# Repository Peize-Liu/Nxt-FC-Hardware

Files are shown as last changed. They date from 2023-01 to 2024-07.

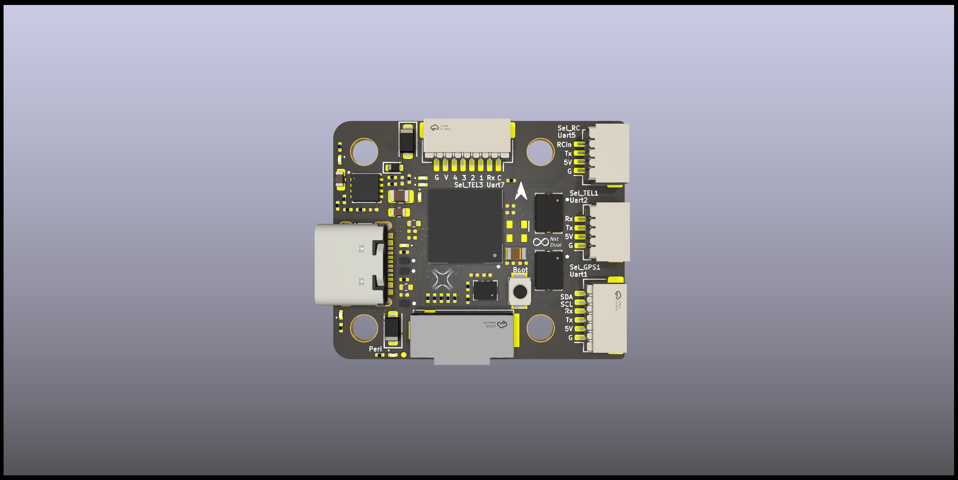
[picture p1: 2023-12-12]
NxtPX4SocketFront.png

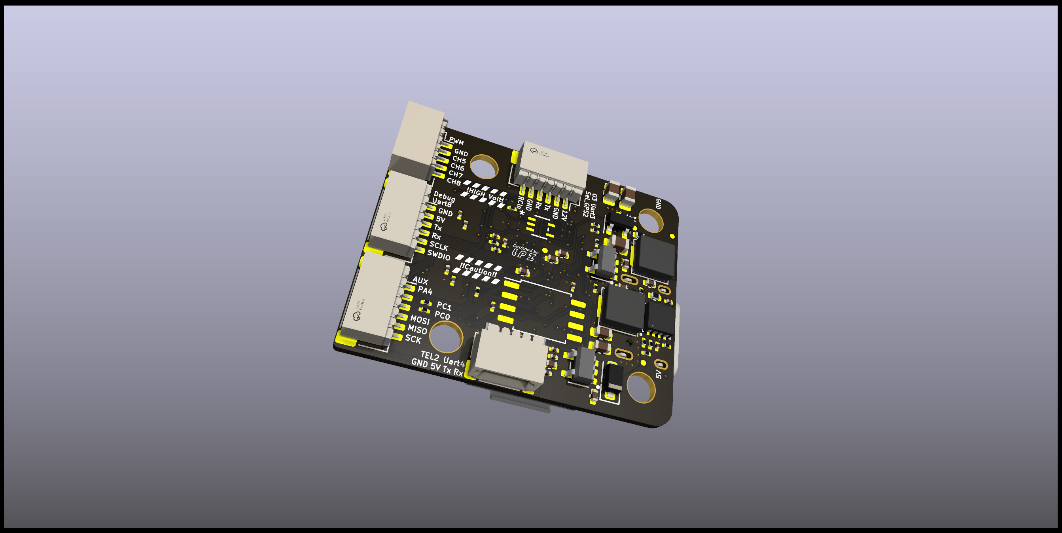
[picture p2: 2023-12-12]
NxtPX4_Back.png

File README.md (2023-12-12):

# NxtPX4-Hardware V2 Dual

* [English](# Getting start)
* [中文](# 配置指南)



## Getting start



### Hardware connection

### Compile PX4 bootloader

### Compile PX4 Firmware

### Config NxtPX4-Dual

## 配置指南



### 电控系统连接

### 编译PX4固件Bootloader

### 编译PX4固件

### 配置你的NxtPX4-Dual

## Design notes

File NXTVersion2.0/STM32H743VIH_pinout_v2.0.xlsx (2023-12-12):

STM32 H743 VIH (2MFlash 1M RAM) LBGA 封装安排不同 |  |  | 系统规定，不方便换PIN
 |  |  | 用户规定，方便换PIN，基本是外部中断和GPIO_Output
Core |  |  |  |  |  |  | 原理图检查 | STM32Cube 检查
IMU | BMI088 |  | SPI1 | MOSI | PA7 |  | v | v
 |  |  |  | MISO | PA6 |  | v | v
 |  |  |  | SCK | PA5 |  | v | v
 |  |  |  | Gyro_CS | PA3 |  | v | v
 |  |  |  | Accel_CS | PA2 |  | v | v
 |  |  |  | Gyro_Data_RDY | PA1 | EXTI1 | v | v
 |  |  |  | Accel_Data_RDY | s | EXTI0 | v | v
 | BMI088 |  | SPI4 | MOSI | PE6 |  | v | v
 |  |  |  | MISO | PE5 |  | v | v
 |  |  |  | SCK | PE2 |  | v | v
 |  |  |  | Gyro_CS | PC2 |  | v | v
 |  |  |  | Accel_CS | PC13 |  | v | v
 |  |  |  | Gyro_Data_RDY | PE3 | EXTI3 | v | v
 |  |  |  | Accel_Data_RDY | PE4 | EXTI4 | v | v
Baro | SPL06-01 |  | I2C1 | SDA | PB7 |  | v | v
 |  |  |  | SCL | PB6 |  | v | v
 |  |  |  | Baro_Data_RDY | PB5 | EXTI5 | v | v
Motor | PWM/DSHOT | CH1 | TIM1 | CH1 | PE9 |  | v | v
 |  | CH2 |  | CH2 | PE11 |  | v | v
 |  | CH3 |  | CH3 | PE13 |  | v | v
 |  | CH4 |  | CH4 | PE14 |  | v | v
 |  | CH5 | TIM2 | CH3 | PB10 |  | v | v
 |  | CH6 |  | CH4 | PB11 |  | v | v
 |  | CH7 | TIM3 | CH3 | PB0 |  | v | v
 |  | CH8 |  | CH4 | PB1 |  | v | v
LSE | 32.768kHz |  | OSC32 | OSC_IN | PC14 |  | v | v
 |  |  |  | OSC_OUT | PC15 |  | v | v
HSE | 16Mhz source |  | OSC | OSC_IN | PH0 |  | v | v
LED | GPIO_OUTPUT |  | Blue |  | PB15 |  | v | v
 |  |  | Red |  | PD15 |  | v | v
 |  |  | Green |  | PD11 |  | v | v
FRAM | W25Q128JVS |  | SPI2 | SCK | PD3 |  | v | v
 |  |  |  | MISO | PB14 |  | v | v
 |  |  |  | MOSI | PC3 |  | v | v
 |  |  |  | CS | PD4 |  | v | v
Connector
SPI |  |  | SPI3 | MOSI | PB2 |  | v | v
 |  |  |  | MISO | PB4 |  | v | v
 |  |  |  | SCK | PB3 |  | v | v
I2C |  |  | I2C4 | SDA | PD13 |  | v | v
 |  |  |  | SCL | PD12 |  | v | v
UART | Debug (GPS3) |  | UART8 | RX | PE0 |  | v | v
 |  |  |  | TX | PE1 |  | v | v
 | Computer (TEL1) |  | UART4 | RX | PB8 |  | v | v
 |  |  |  | TX | PB9 |  | v | v
 | RC_input(RC) |  |  | Sbus INV | PD14 |  | v | v
 |  |  | UART5 | RX | PB12 |  | v | v
 |  |  |  | TX | PB13 |  | v | v
 | Debug (NC) |  | UART6 | RX | PC7 |  | v | No hardware connection support
 |  |  |  | TX | PC6 |  | v
 | ESC_tele(TEL2) |  | UART7 | RX | PE7 |  | v | v
 |  |  |  | TX | PE8 | NC | v | v
 |  |  | USART1 | CK | PA8 | NC | v
 | GPS1 |  |  | TX | PA9 |  | v | v
 |  |  |  | RX | PA10 |  | v | v
 |  |  | USART2 | CK | PD7 | NC | v
 | GPS2 |  |  | TX | PD5 |  | v | v
 |  |  |  | RX | PD6 |  | v | v
 |  |  | USART3 | CK | PD10 | NC | v
 | TEL3 |  |  | TX | PD8 |  | v | v
 |  |  |  | RX | PD9 |  | v | v
USB_FS |  |  | USB | FS_DM | PA11 |  | v | v
 |  |  |  | FS_DP | PA12 |  | v | v
SD |  |  | SDMMC1 | D0 | PC8 |  | v | v
 |  |  |  | D1 | PC9 |  | v | v
 |  |  |  | D2 | PC10 |  | v | v
 |  |  |  | D3 | PC11 |  | v | v
 |  |  |  | CK | PC12 |  | v | v
 |  |  |  | CMD | PD2 |  | v | v
Debug |  |  | SWD | SWDIO | PA13 |  | v | v
 |  |  |  | SWCLK | PA14 |  | v | v
Battery |  |  | ADC1_INP4 | BAT_V | PC4 |  | v | v
 |  |  | ADC2_INP8 | BAT_I | PC5 |  | v | v
USB Detection |  |  | Input |  | PD0 |  | v | v
AUX_GPIO |  |  |  | AUX1 | PC0 |  | v | v
 |  |  |  | AUX2 | PC1 |  | v | v
 |  |  |  | AUX3 | PA4 |  | v | v

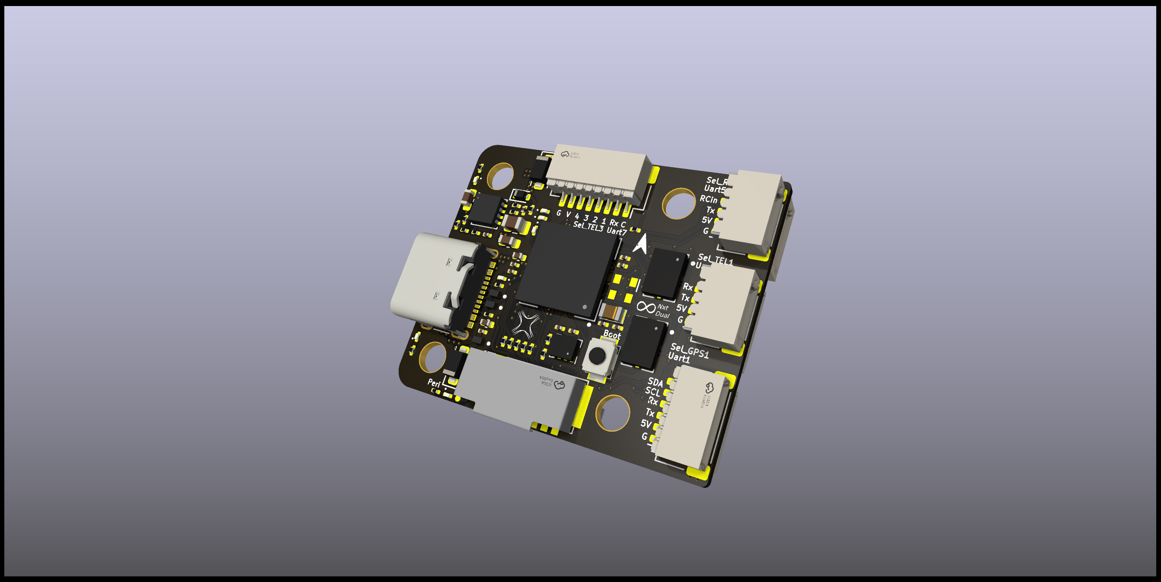
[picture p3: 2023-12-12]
NxtPX4_Front.png

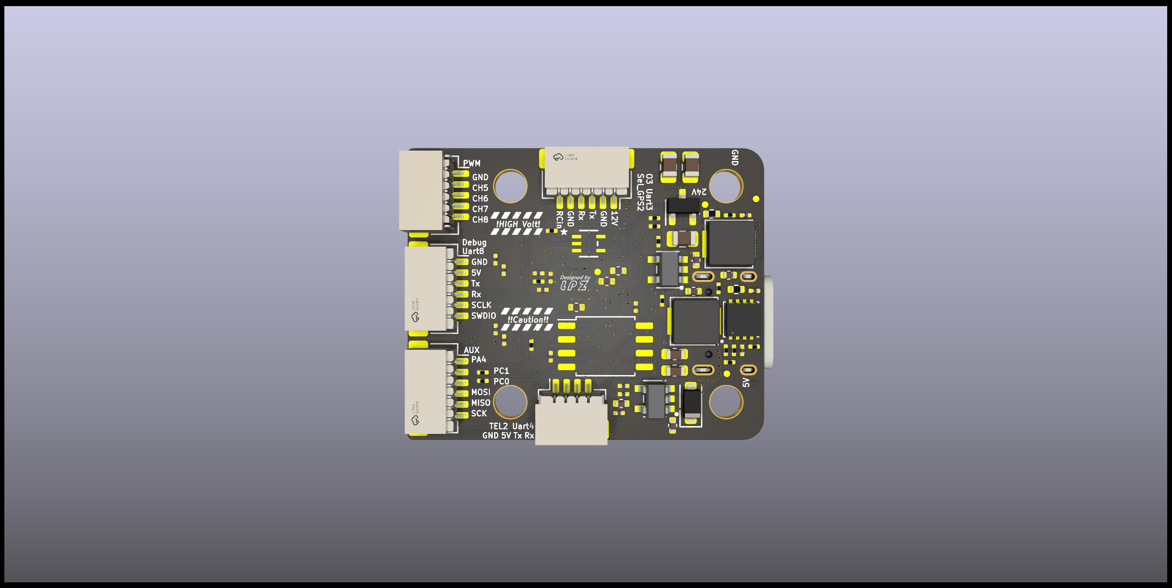
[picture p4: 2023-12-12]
NxtPX4SocketBack.png

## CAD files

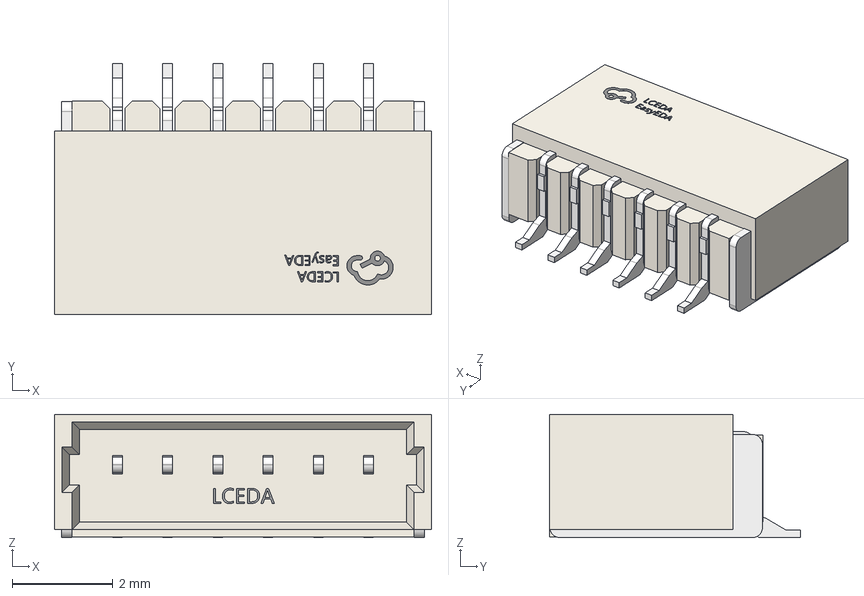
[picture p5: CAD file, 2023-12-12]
NxtFC-DUAL/project_lib/3D_Model/sh1.0_6pin_hori.step
7.50 x 5.00 x 2.45 mm

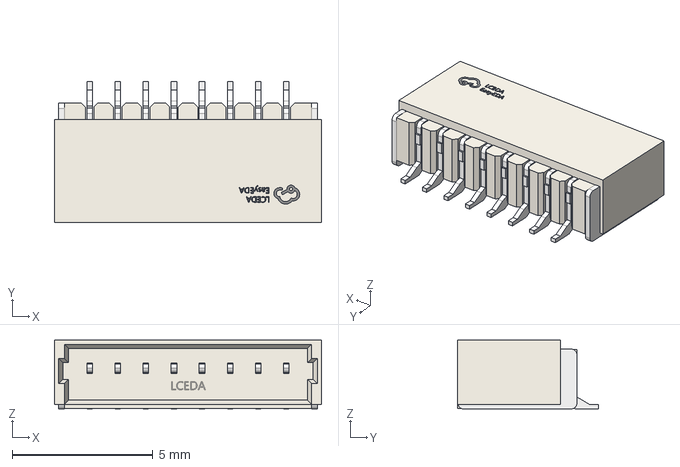
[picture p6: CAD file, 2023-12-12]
NxtFC-DUAL/project_lib/3D_Model/sh1.0_8p_hori.step
9.50 x 5.00 x 2.45 mm

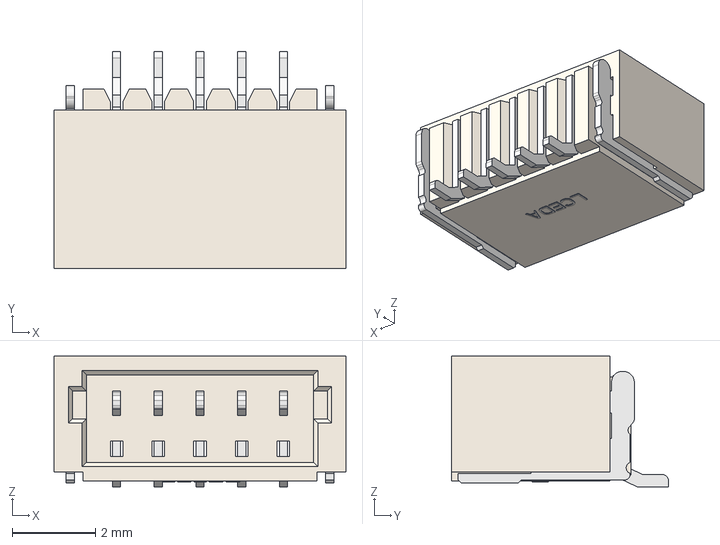
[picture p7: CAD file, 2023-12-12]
NxtFC-DUAL/project_lib/3D_Model/sh1.0_5pin_hori.step
7.00 x 5.20 x 3.14 mm

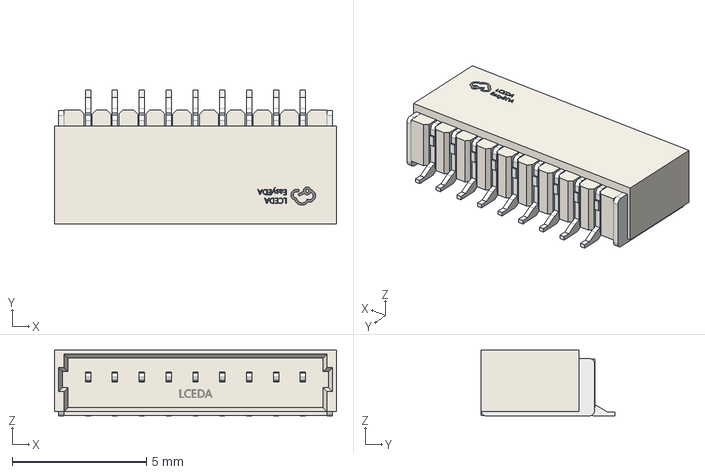
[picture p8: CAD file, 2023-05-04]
NxtFC-DUAL/project_lib/3D_Model/sh1.0_01x09_hori.step
10.5 x 5.00 x 2.45 mm

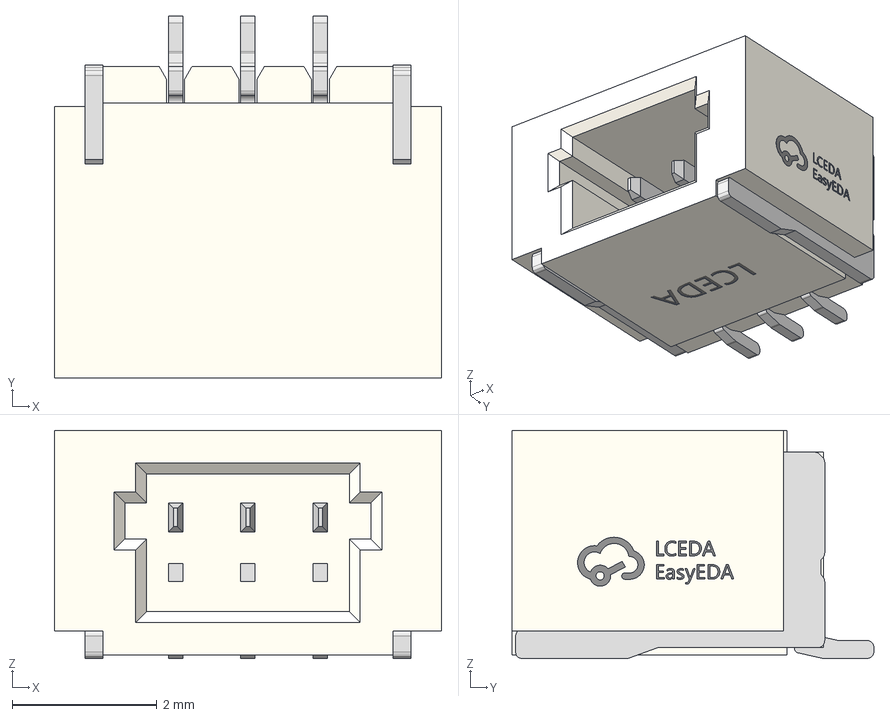
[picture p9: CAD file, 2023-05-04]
NxtFC-DUAL/project_lib/3D_Model/sh1.0_3pin_hor.step
5.35 x 5.00 x 3.15 mm

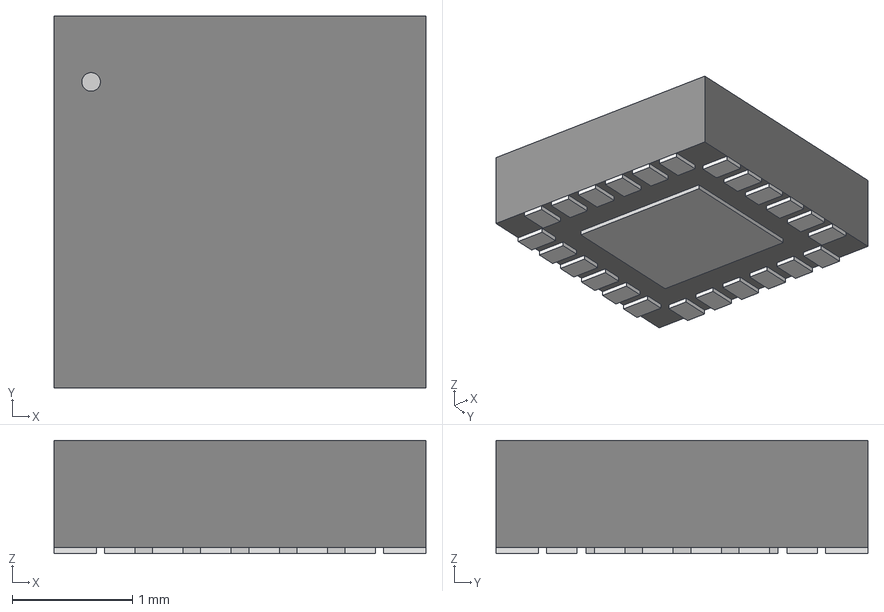
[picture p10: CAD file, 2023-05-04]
NxtFC-DUAL/project_lib/3D_Model/QFN24_3X3X0P9_IVS_ICM20649.step
3.10 x 3.10 x 0.942 mm

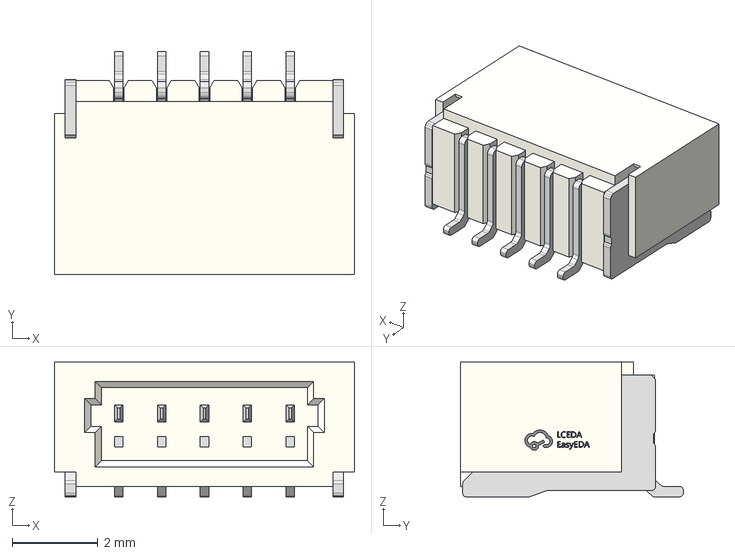
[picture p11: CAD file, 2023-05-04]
NxtFC-DUAL/project_lib/3D_Model/01x05_sh1.0_hori.step
7.00 x 5.20 x 3.15 mm

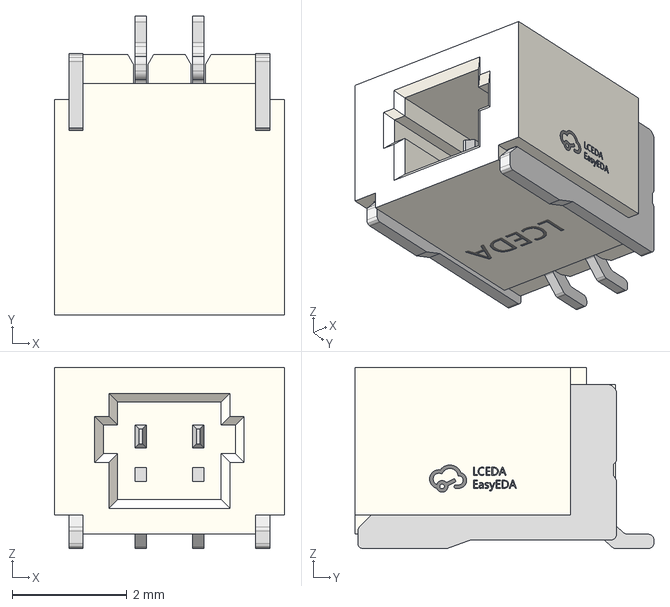
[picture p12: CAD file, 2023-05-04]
NxtFC-DUAL/project_lib/3D_Model/sh1.0_01x02p_hori.step
4.00 x 5.20 x 3.15 mm

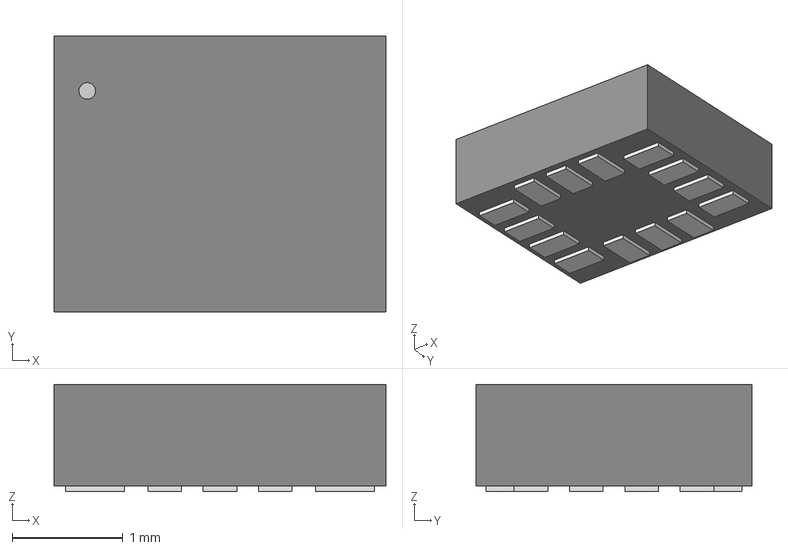
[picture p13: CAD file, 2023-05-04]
NxtFC-DUAL/project_lib/3D_Model/LGA14_2P5X3X0P91_IVS_ICM42688-P .step
3.00 x 2.49 x 0.968 mm

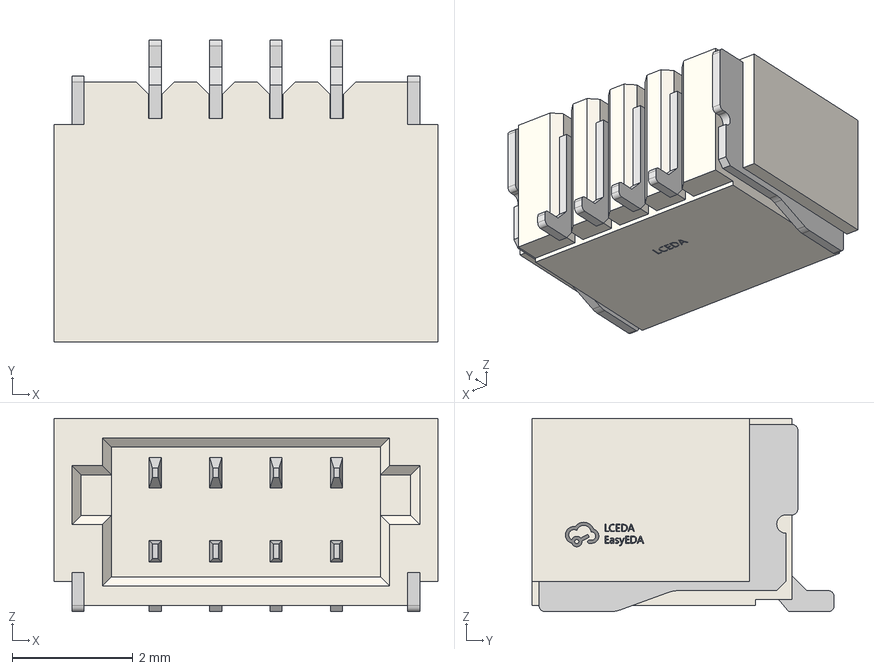
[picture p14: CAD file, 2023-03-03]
NxtFC-DUAL/project_lib/3D_Model/sh1.0_4p.step
6.35 x 5.00 x 3.20 mm

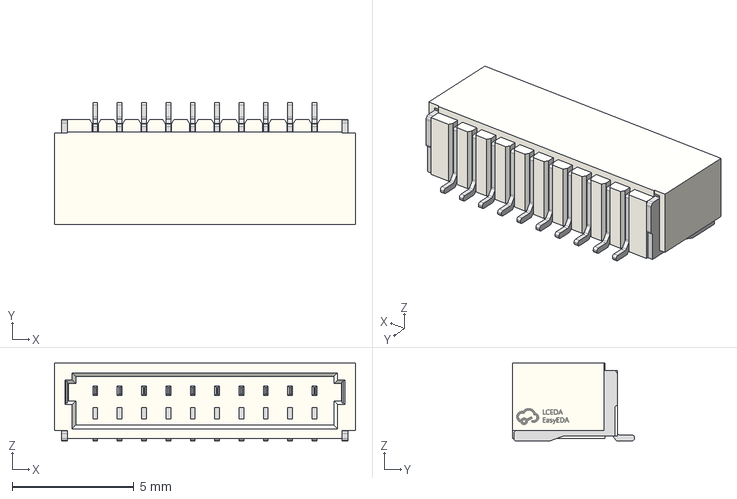
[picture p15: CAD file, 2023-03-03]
NxtFC-DUAL/project_lib/3D_Model/sh1.0_10P.step
12.4 x 5.00 x 3.20 mm

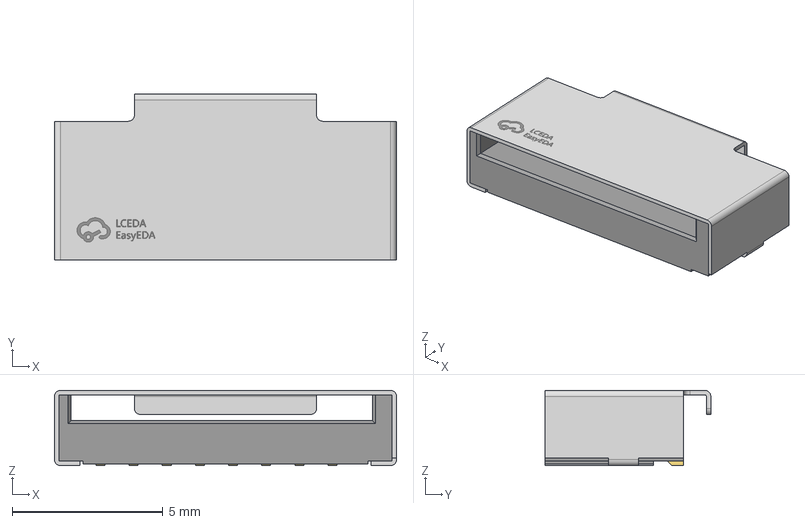
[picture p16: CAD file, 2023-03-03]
NxtFC-DUAL/project_lib/3D_Model/sd_card.step
11.4 x 5.50 x 2.50 mm

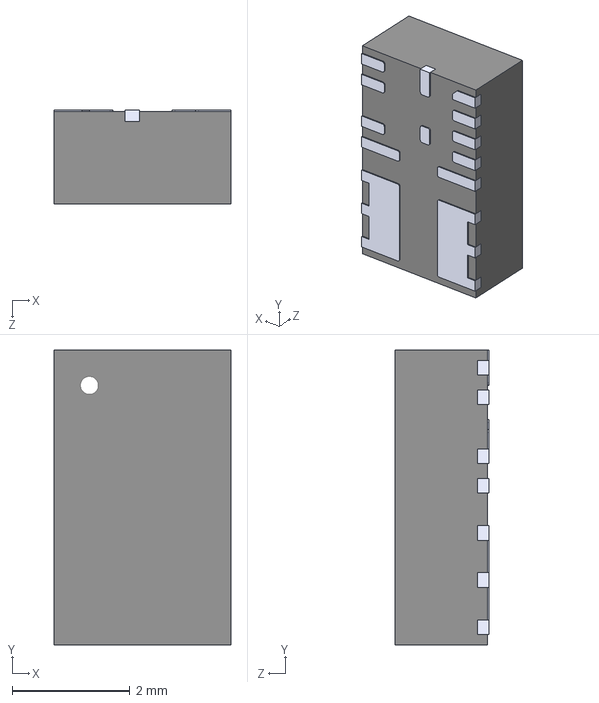
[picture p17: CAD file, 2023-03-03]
NxtFC-DUAL/project_lib/3D_Model/MPM3515GQV-AEC1 (QFN-17, 3x5x1.6).step
3.00 x 5.00 x 1.60 mm

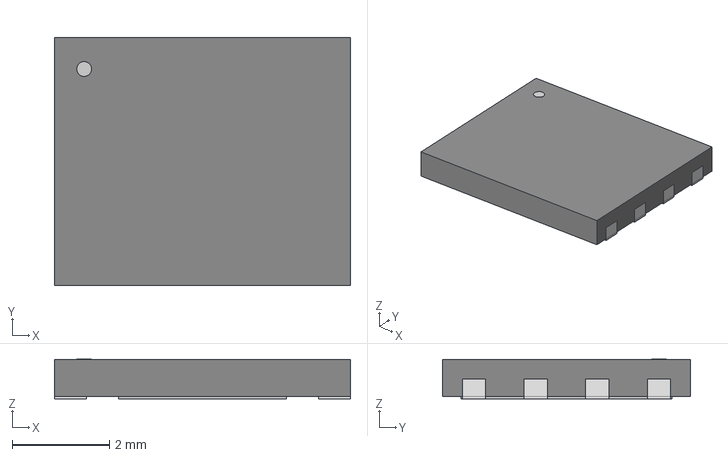
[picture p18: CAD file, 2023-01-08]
NxtFC-DUAL/project_lib/3D_Model/WSON-8_6X5_WIN.step
6.10 x 5.11 x 0.815 mm

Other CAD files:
NxtFC-DUAL/project_lib/3D_Model/CAP_ABS07-32_768KHZ-T_ABR.step
NxtFC-DUAL/project_lib/3D_Model/DFN1006-2_SOD882_NEX.step
NxtFC-DUAL/project_lib/3D_Model/QFN_BMP388_BOS.step
NxtFC-DUAL/project_lib/3D_Model/CSP-USC16-TR--3DModel-STEP-468060.STEP
NxtFC-DUAL/project_lib/3D_Model/QFN8_3X3_MPS.step
NxtFC-DUAL/project_lib/3D_Model/SG-210STF25_0000ML3_EPS.step
NxtFC-DUAL/project_lib/3D_Model/SOT-23-5_RIT.step
NxtFC-DUAL/project_lib/3D_Model/TFBGA100.step

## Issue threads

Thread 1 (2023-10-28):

ETH support planned?

petergerten, 2023-10-28:
Hi,

great project!
Any plans for a revision with ethernet mac support for fast communication with companion computer?

Peter

Peize-Liu, 2023-10-28:
Hello,
Thank you for your advice, current version provides IMU message at 500Hz using maximum baudrate. The maximum control rate and message rate are limited by MCU frequncy and also PX4 firmware. I don't think there is a need for ethernet mac in Nxt, because of the PCB size and also the task of our research. But if there is a need for that, I may seek for some cooperation to achive that.

Closed 2023-10-28.

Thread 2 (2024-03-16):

你好，为什么在第二个版本中没有使用icm42688 ，而是使用两个bmi088

deepuav, 2024-03-16:
从参数上看icm42688 要优于 bmi088啊，是不是不稳定啊？

Peize-Liu, 2024-03-17:
ICM 系列都挺容易震傻，BMI088 测下来在当前我们所有的飞机结构上，数据更好一些

deepuav, 2024-03-20:
感谢大神回复。这边pps输入捕获功能和相机触发移植的怎么样啊？有测试过吗？

Peize-Liu, 2024-03-20:
> 感谢大神回复。这边pps输入捕获功能和相机触发移植的怎么样啊？有测试过吗？

没有这样搞过，如果PX4 固件支持的话，硬件上应该只要有可以使用的GPIO都是可以的，我们系统IMU和相机不是同步的，所以没有特别考虑过

deepuav, 2024-03-20:
我这边在您第二版的基础上加了一个adis16470，把一个bmi088换成了icm42686 。想做板子测试一下，需要您这边许可吗？

deepuav, 2024-03-20:
>
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

deepuav, 2024-03-20:
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

deepuav, 2024-03-20:
回头我把kicad工程，也发上来

deepuav, 2024-03-21:
13176502829 我把工程文件打包发给你

hcws, 2025-08-09:
Thank you for your contribution. May I ask why the BOM and Gerber files for version V2 were not generated?

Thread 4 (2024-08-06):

v1.2.0 schematics

raimapo, 2024-08-06:
Hello,

Will You provide v1.2.0 schematics and PCB. I will be glad to test this autopilot, but I need to change connectors which could be more suitable for my project. Thank You.

Raimondas

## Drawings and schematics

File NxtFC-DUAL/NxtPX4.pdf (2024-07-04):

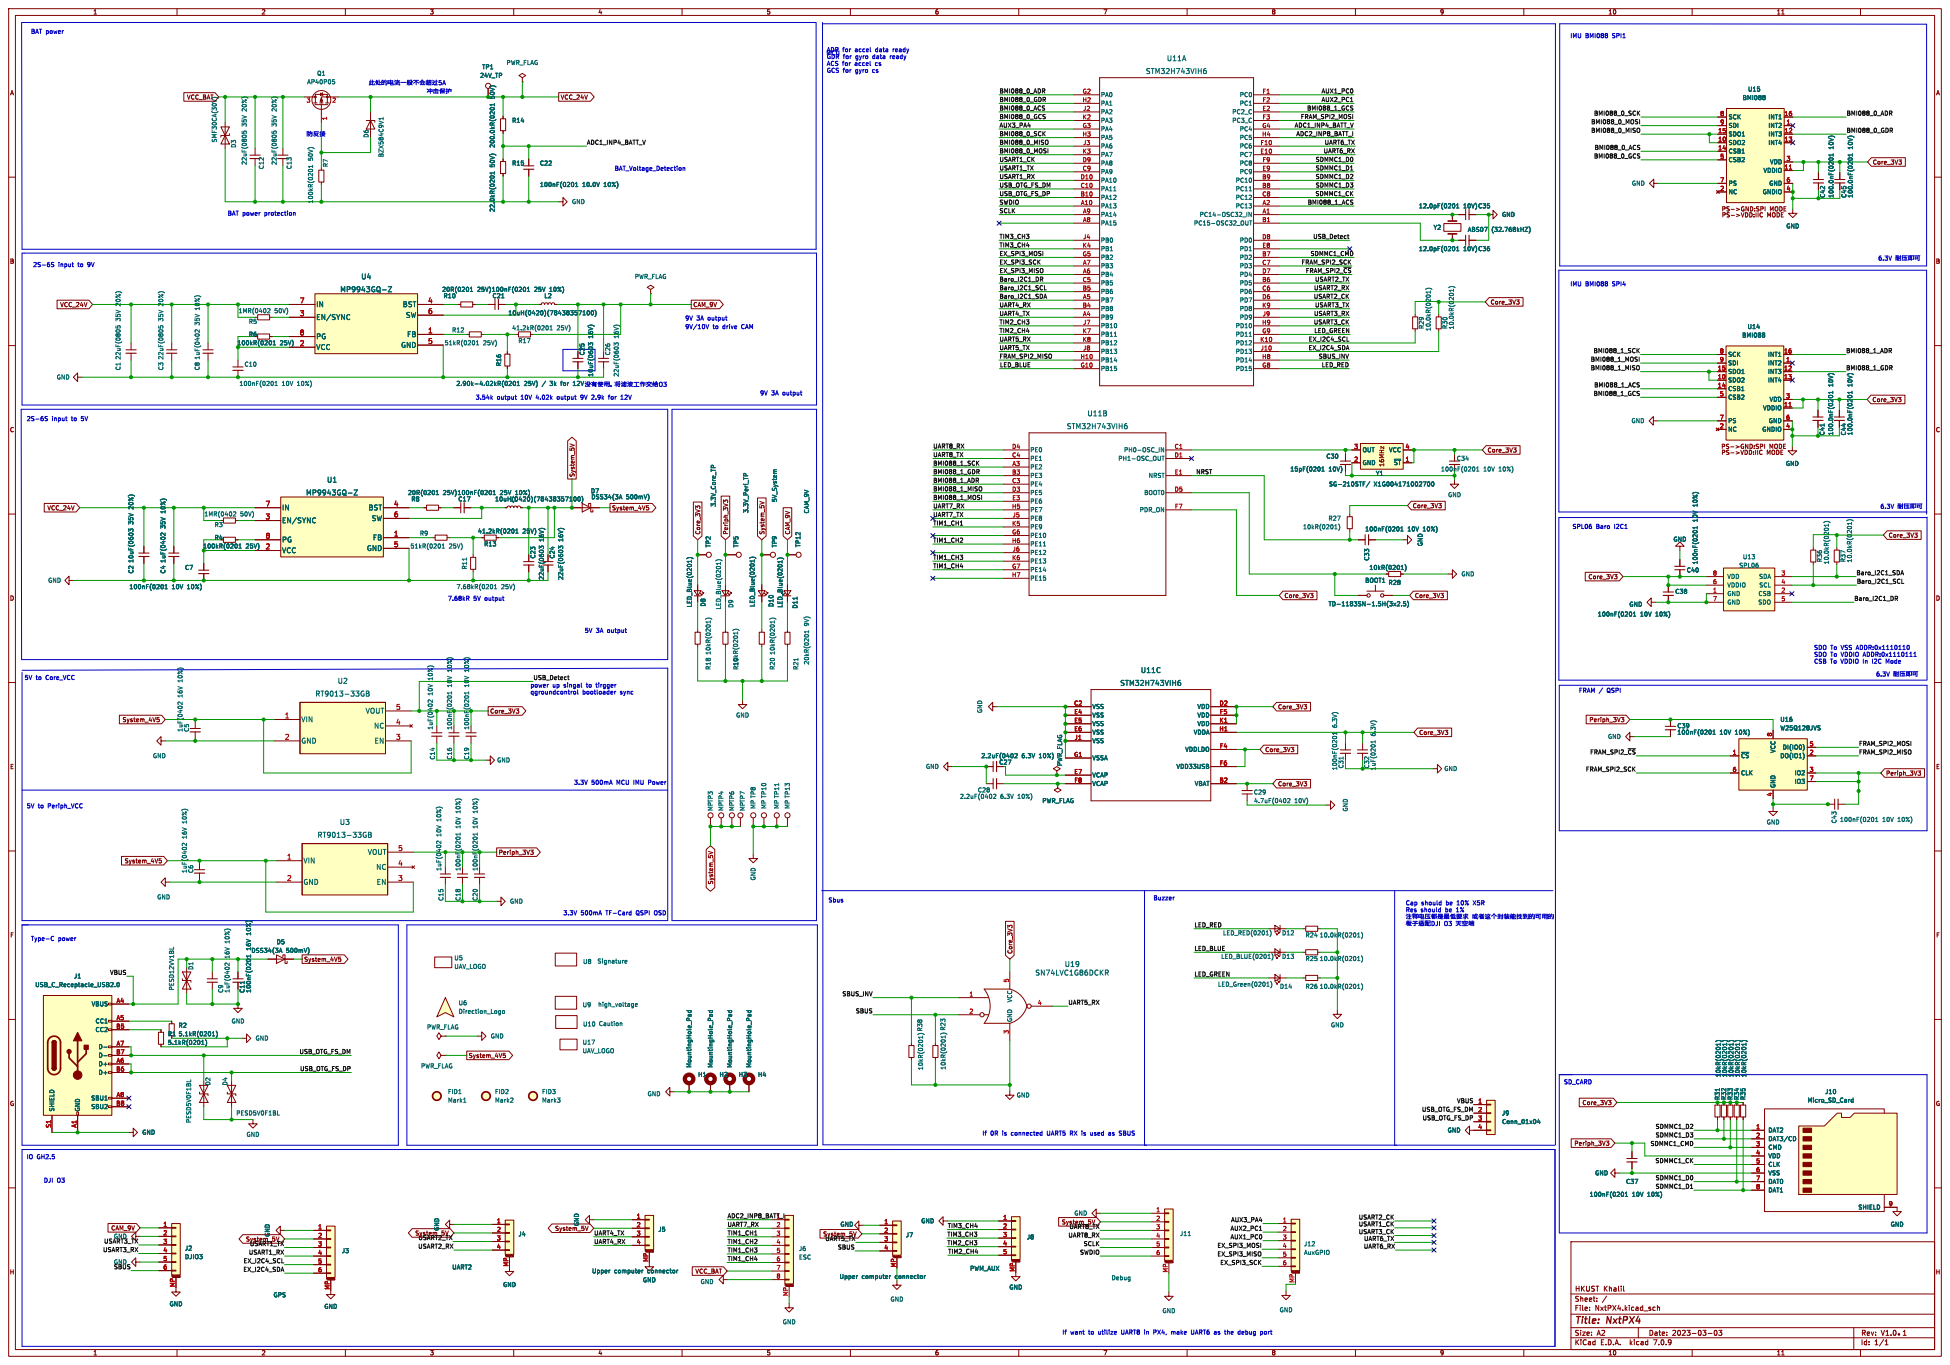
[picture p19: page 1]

ADR for accel data ready GDR for gyro data ready ACS for accel cs GCS for gyro cs
MCU

9V 3A output þÿl¡g O•u(ÿ\nälâ]åO\N¤~ÙO3

SDO To VSS ADDR:0x1110110 SDO To VDDIO ADDR:0x1110111 CSB To VDDIO In I2C Mode

power up singal to tirgger

Cap should be 10% X5R
Res should be 1%
þÿlè‘Êu5S‹•ýf/gON‰•lB þÿb€•ÙN*\ˆÅ€ýb~R0v„Sïu(v„
þÿg•[P•-

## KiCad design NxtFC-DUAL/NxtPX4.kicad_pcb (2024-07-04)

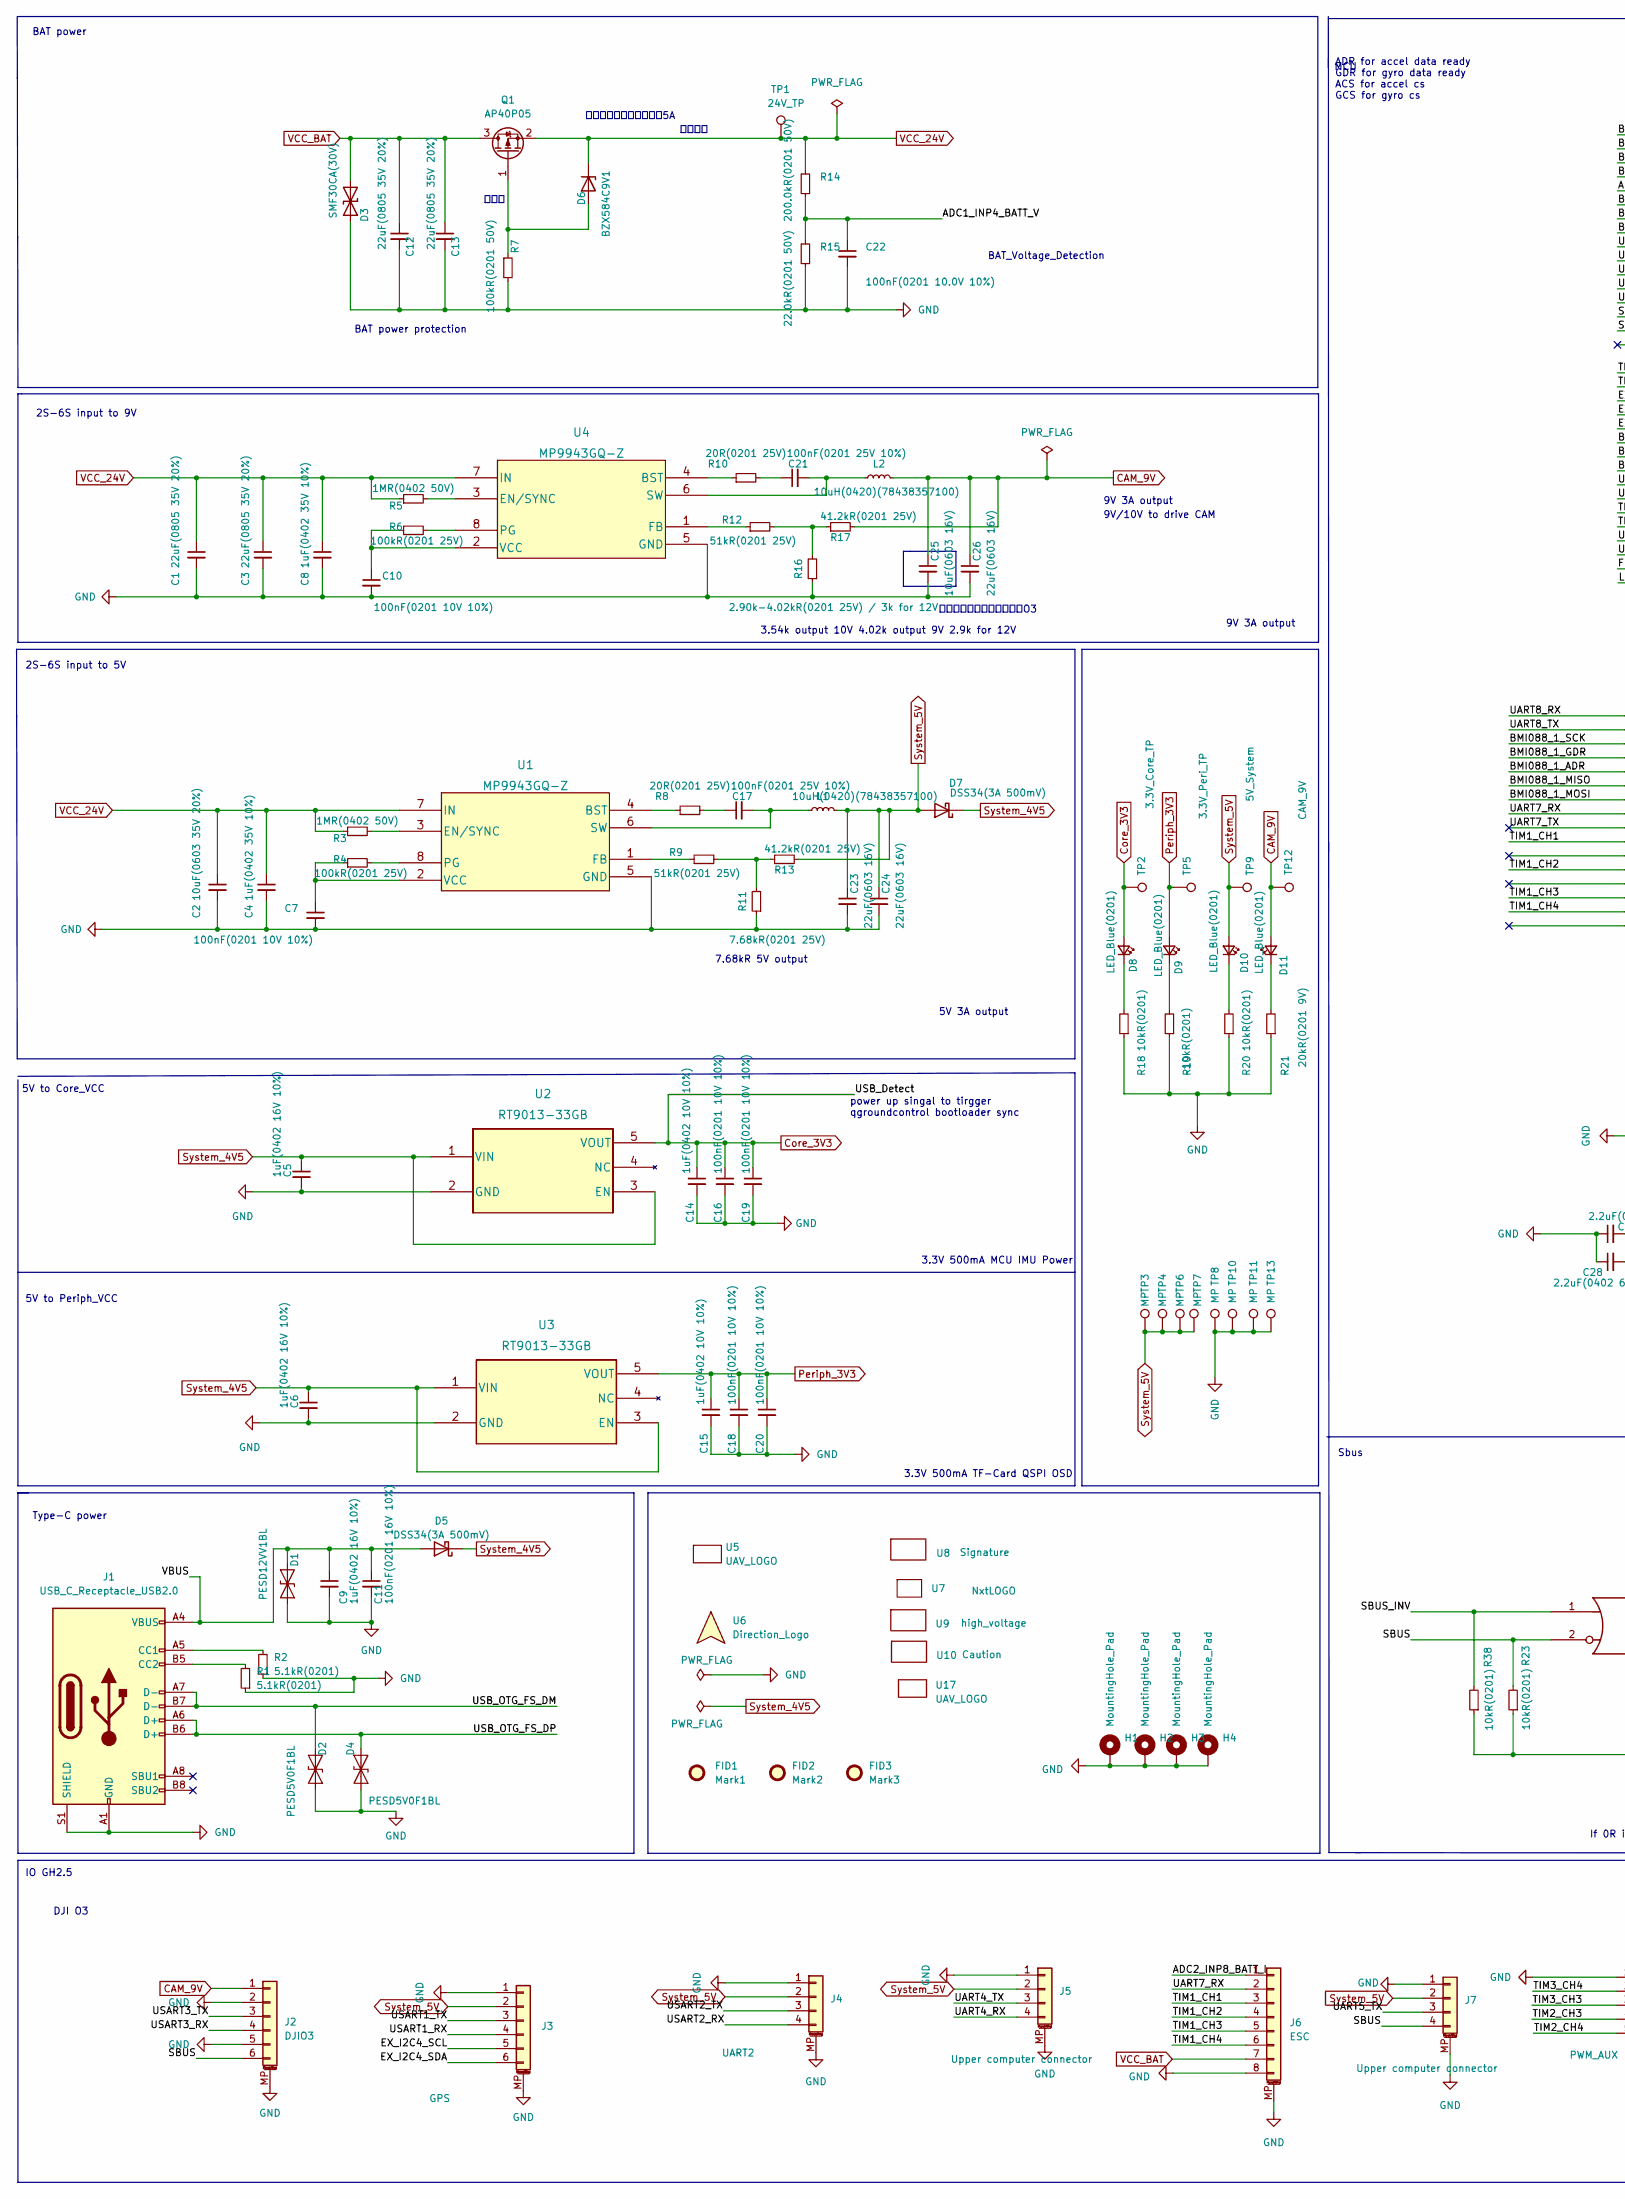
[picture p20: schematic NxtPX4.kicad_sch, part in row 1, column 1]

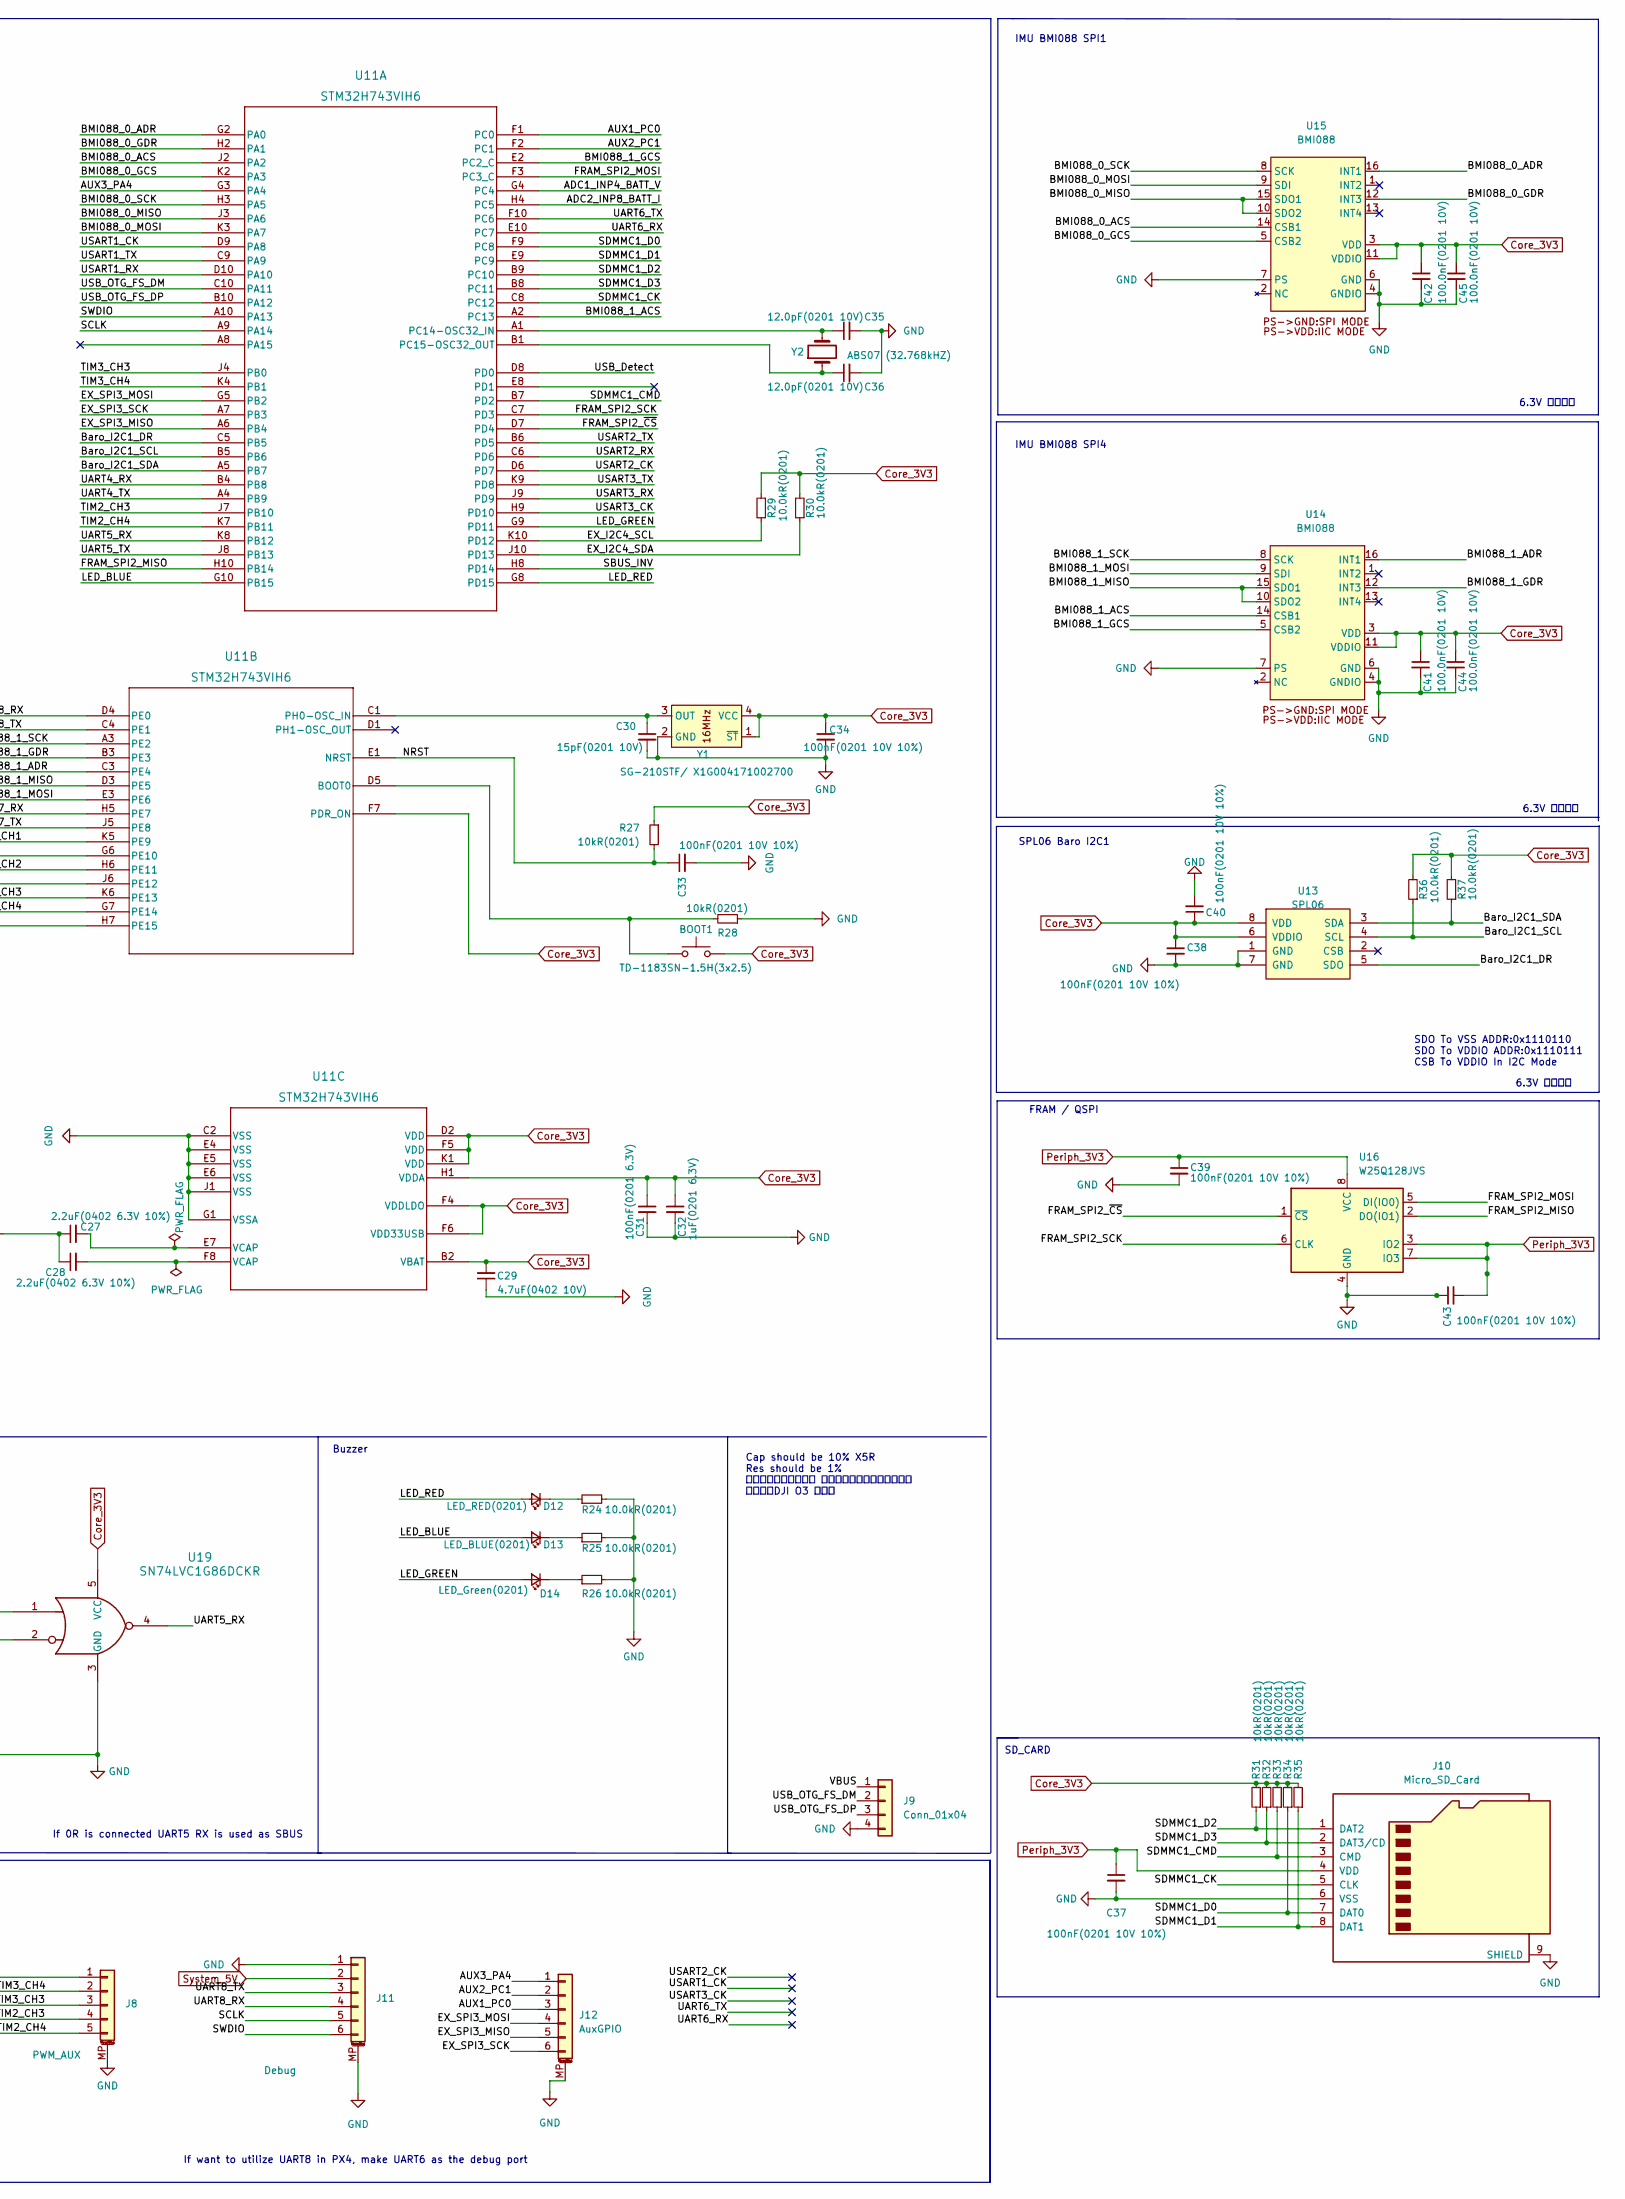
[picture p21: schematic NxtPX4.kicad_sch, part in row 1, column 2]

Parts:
BOOT1: TD-1183SN-1.5H(3x2.5); 3x2.5PushButton
C1, C3, C12, C13: 22uF(0805 35V 20%); C_0805_2012Metric
C2: 10uF(0603 35V 20%); C_0603_1608Metric
C4, C8: 1uF(0402 35V 10%); C_0402_1005Metric
C5, C6, C9: 1uF(0402 16V 10%); C_0402_1005Metric
C7, C10, C16, C18, C19, C20, C33, C34, C37, C38, C39, C40, C43: 100nF(0201 10V 10%); C_0201_0603Metric
C11: 100nF(0201 16V 10%); C_0201_0603Metric
C14, C15: 1uF(0402 10V 10%); C_0402_1005Metric
C17, C21: 100nF(0201 25V 10%); C_0201_0603Metric
C22: 100nF(0201 10.0V 10%); C_0201_0603Metric
C23, C24, C26: 22uF(0603 16V); C_0603_1608Metric
C25: 10uF(0603 16V); C_0603_1608Metric
C27, C28: 2.2uF(0402 6.3V 10%); C_0402_1005Metric
C29: 4.7uF(0402 10V); C_0402_1005Metric
C30: 15pF(0201 10V); C_0201_0603Metric
C31: 100nF(0201 6.3V); C_0201_0603Metric
C32: 1uF(0201 6.3V); C_0201_0603Metric
C35, C36: 12.0pF(0201 10V); C_0201_0603Metric
C41, C42, C44, C45: 100.0nF(0201 10V); C_0201_0603Metric
D1: PESD12VV1BL; PESD12VV1BL_315
D2, D4: PESD5V0F1BL
D3: SMF30CA(30V); D_SOD-123F
D5, D7: DSS34(3A 500mV); D_SOD-123F
D6: BZX584C9V1; D_SOD-523
D8, D9, D10, D11: LED_Blue(0201); LED_0201_0603Metric
D12: LED_RED(0201); LED_0201_0603Metric
D13: LED_BLUE(0201); LED_0201_0603Metric
D14: LED_Green(0201); LED_0201_0603Metric
FID1: Mark1; Fidiucial
FID2: Mark2; Fidiucial
FID3: Mark3; Fidiucial
H1, H2, H3, H4: MountingHole_Pad; M2MountingHole
J1: USB_C_Receptacle_USB2.0; USB_C_Small
J2: DJIO3; 1x06-1MP_P1.00mm_Horizontal
J3: GPS; 1x06-1MP_P1.00mm_Horizontal
J4: UART2; 01x04_MP_sh1.0_Hori
J5, J7: Upper computer connector; 01x04_MP_sh1.0_Hori
J6: ESC; 01x08_MP_sh1.0_Hori
J8: PWM_AUX; 01x05_MP_sh1.0_Hori
J9: Conn_01x04; Conn_4Pin
J10: Micro_SD_Card; TF-SMD_TF-021B-H265
J11: Debug; 1x06-1MP_P1.00mm_Horizontal
J12: AuxGPIO; 1x06-1MP_P1.00mm_Horizontal
L1, L2: 10uH(0420)(78438357100); Inductor_0420
Q1: AP40P05; SOT-23
R1, R2: 5.1kR(0201); R_0201_0603Metric
R3, R5: 1MR(0402 50V); R_0402_1005Metric
R4, R6: 100kR(0201 25V); R_0201_0603Metric
R7: 100kR(0201 50V); R_0201_0603Metric
R8, R10: 20R(0201 25V); R_0201_0603Metric
R9, R12: 51kR(0201 25V); R_0201_0603Metric
R11: 7.68kR(0201 25V); R_0201_0603Metric
R13, R17: 41.2kR(0201 25V); R_0201_0603Metric
R14: 200.0kR(0201 50V); R_0201_0603Metric
R15: 22.0kR(0201 50V); R_0201_0603Metric
R16: 2.90k-4.02kR(0201 25V) / 3k for 12V; R_0201_0603Metric
R18, R19, R20, R23, R27, R28, R31, R32, R33, R34, R35, R38: 10kR(0201); R_0201_0603Metric
R21: 20kR(0201 9V); R_0201_0603Metric
R24, R25, R26, R29, R30, R36, R37: 10.0kR(0201); R_0201_0603Metric
TP1: 24V_TP; MiniTP
TP2: 3.3V_Core_TP; MiniTP
TP3, TP4, TP6, TP7, TP8, TP10, TP11, TP13: MP; PWR_Circle
TP5: 3.3V_Peri_TP; MiniTP
TP9: 5V_System; MiniTP
TP12: CAM_9V; MiniTP
U1, U4: MP9943GQ-Z
U2, U3: RT9013-33GB
U5: UAV_LOGO; Uav_logo
U6: Direction_Logo
U7: NxtLOGO
U8: Signature; my_signature
U9: high_voltage
U10: Caution
U11: STM32H743VIH6; STM32H743VIHBGA100C80P10X10_800X800X110N
U13: SPL06; Bosch_LGA-8_2x2.5mm_P0.65mm_ClockwisePinNumbering
U14, U15: BMI088
U16: W25Q128JVS; SOIC-8_5.23x5.23mm_P1.27mm
U17: UAV_LOGO; Dual_logo
U19: SN74LVC1G86DCKR; DCK5
Y1: SG-210STF/ X1G004171002700; Oscillator_SMD_Abracon_ASDMB-4Pin_2.5x2.0mm
Y2: ABS07 (32.768kHZ); LSE(2012)

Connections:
/ADC1_INP4_BATT_V: C22.1, R14.2, R15.1, U11.G4 (PC4)
/ADC2_INP8_BATT_I: J6.1, U11.H4 (PC5)
/AUX1_PC0: J12.3, U11.F1 (PC0)
/AUX2_PC1: J12.2, U11.F2 (PC1)
/AUX3_PA4: J12.1, U11.G3 (PA4)
/BMI088_0_ACS: U11.J2 (PA2), U15.14 (CSB1)
/BMI088_0_ADR: U11.G2 (PA0), U15.16 (INT1)
/BMI088_0_GCS: U11.K2 (PA3), U15.5 (CSB2)
/BMI088_0_GDR: U11.H2 (PA1), U15.12 (INT3)
/BMI088_0_MISO: U11.J3 (PA6), U15.10 (SDO2), U15.15 (SDO1)
/BMI088_0_MOSI: U11.K3 (PA7), U15.9 (SDI)
/BMI088_0_SCK: U11.H3 (PA5), U15.8 (SCK)
/BMI088_1_ACS: U11.A2 (PC13), U14.14 (CSB1)
/BMI088_1_ADR: U11.C3 (PE4), U14.16 (INT1)
/BMI088_1_GCS: U11.E2 (PC2_C), U14.5 (CSB2)
/BMI088_1_GDR: U11.B3 (PE3), U14.12 (INT3)
/BMI088_1_MISO: U11.D3 (PE5), U14.10 (SDO2), U14.15 (SDO1)
/BMI088_1_MOSI: U11.E3 (PE6), U14.9 (SDI)
/BMI088_1_SCK: U11.A3 (PE2), U14.8 (SCK)
/Baro_I2C1_DR: U11.C5 (PB5), U13.5 (SDO)
/Baro_I2C1_SCL: R36.1, U11.B5 (PB6), U13.4 (SCL)
/Baro_I2C1_SDA: R37.1, U11.A5 (PB7), U13.3 (SDA)
/EX_I2C4_SCL: J3.5, R29.1, U11.K10 (PD12)
/EX_I2C4_SDA: J3.6, R30.1, U11.J10 (PD13)
/EX_SPI3_MISO: J12.5, U11.A6 (PB4)
/EX_SPI3_MOSI: J12.4, U11.G5 (PB2)
/EX_SPI3_SCK: J12.6, U11.A7 (PB3)
/FRAM_SPI2_MISO: U11.H10 (PB14), U16.2 (DO(IO1))
/FRAM_SPI2_MOSI: U11.F3 (PC3_C), U16.5 (DI(IO0))
/FRAM_SPI2_SCK: U11.C7 (PD3), U16.6 (CLK)
/FRAM_SPI2_~CS: U11.D7 (PD4), U16.1 (~CS)
/LED_BLUE: D13.2 (A), U11.G10 (PB15)
/LED_GREEN: D14.2 (A), U11.G9 (PD11)
/LED_RED: D12.2 (A), U11.G8 (PD15)
/NRST: C33.1, R27.2, U11.E1 (NRST)
/SBUS: J2.6, J7.4, R23.2, U19.2
/SBUS_INV: R38.2, U11.H8 (PD14), U19.1
/SCLK: J11.5, U11.A9 (PA14)
/SDMMC1_CK: J10.5 (CLK), U11.C8 (PC12)
/SDMMC1_CMD: J10.3 (CMD), R33.1, U11.B7 (PD2)
/SDMMC1_D0: J10.7 (DAT0), R34.1, U11.F9 (PC8)
/SDMMC1_D1: J10.8 (DAT1), R35.1, U11.E9 (PC9)
/SDMMC1_D2: J10.1 (DAT2), R31.1, U11.B9 (PC10)
/SDMMC1_D3: J10.2 (DAT3/CD), R32.1, U11.B8 (PC11)
/SWDIO: J11.6, U11.A10 (PA13)
/TIM1_CH1: J6.3, U11.K5 (PE9)
/TIM1_CH2: J6.4, U11.H6 (PE11)
/TIM1_CH3: J6.5, U11.K6 (PE13)
/TIM1_CH4: J6.6, U11.G7 (PE14)
/TIM2_CH3: J8.4, U11.J7 (PB10)
/TIM2_CH4: J8.5, U11.K7 (PB11)
/TIM3_CH3: J8.3, U11.J4 (PB0)
/TIM3_CH4: J8.2, U11.K4 (PB1)
/UART4_RX: J5.4, U11.B4 (PB8)
/UART4_TX: J5.3, U11.A4 (PB9)
/UART5_RX: U11.K8 (PB12), U19.4
/UART5_TX: J7.3, U11.J8 (PB13)
/UART6_RX: U11.E10 (PC7)
/UART6_TX: U11.F10 (PC6)
/UART7_RX: J6.2, U11.H5 (PE7)
/UART7_TX: U11.J5 (PE8)
/UART8_RX: J11.4, U11.D4 (PE0)
/UART8_TX: J11.3, U11.C4 (PE1)
/USART1_CK: U11.D9 (PA8)
/USART1_RX: J3.4, U11.D10 (PA10)
/USART1_TX: J3.3, U11.C9 (PA9)
/USART2_CK: U11.D6 (PD7)
/USART2_RX: J4.4, U11.C6 (PD6)
/USART2_TX: J4.3, U11.B6 (PD5)
/USART3_CK: U11.H9 (PD10)
/USART3_RX: J2.4, U11.J9 (PD9)
/USART3_TX: J2.3, U11.K9 (PD8)
/USB_OTG_FS_DM: D2.2 (A2), J1.A7 (D-), J1.B7 (D-), J9.2, U11.C10 (PA11)
/USB_OTG_FS_DP: D4.2 (A2), J1.A6 (D+), J1.B6 (D+), J9.3, U11.B10 (PA12)
/VBUS: C9.1, C11.1, D1.2 (A2), D5.2 (A), J1.A4 (VBUS), J1.A9 (VBUS), J1.B4 (VBUS), J1.B9 (VBUS), J9.1
CAM_9V: C25.1, C26.1, D11.2 (A), J2.1, L2.2, R17.2, TP12.1
Core_3V3: BOOT1.1, C14.1, C16.1, C19.1, C29.2, C31.1, C32.1, C34.1, C38.1, C40.1, C41.1, C42.1, C44.1, C45.1, D8.2 (A), R27.1, R29.2, R30.2, R31.2, R32.2, R33.2, R34.2, R35.2, R36.2, R37.2, TP2.1, U2.5 (VOUT), U11.B2 (VBAT), U11.D2 (VDD), U11.D8 (PD0), U11.F4 (VDDLDO), U11.F5 (VDD), U11.F6 (VDD33USB), U11.F7 (PDR_ON), U11.H1 (VDDA), U11.K1 (VDD), U13.6 (VDDIO), U13.8 (VDD), U14.3 (VDD), U14.11 (VDDIO), U15.3 (VDD), U15.11 (VDDIO), U19.5 (VCC), Y1.1 (~ST), Y1.4 (VCC)
GND: C1.2, C2.2, C3.2, C4.2, C5.2, C6.2, C7.2, C8.2, C9.2, C10.2, C11.2, C12.2, C13.2, C14.2, C15.2, C16.2, C18.2, C19.2, C20.2, C22.2, C23.2, C24.2, C25.2, C26.2, C27.1, C28.1, C29.1, C30.2, C31.2, C32.2, C33.2, C34.2, C35.2, C36.2, C37.2, C38.2, C39.2, C40.2, C41.2, C42.2, C43.1, C44.2, C45.2, D1.1 (A1), D2.1 (A1), D3.1 (A1), D4.1 (A1), H1.1, H2.1, H3.1, H4.1, J1.A1 (GND), J1.A12 (GND), J1.B1 (GND), J1.B12 (GND), J1.S1 (SHIELD), J2.2, J2.5, J2.MP (MountPin), J3.1, J3.MP (MountPin), J4.1, J4.MP (MountPin), J5.1, J5.MP (MountPin), J6.8, J6.MP (MountPin), J7.1, J7.MP (MountPin), J8.1, J8.MP (MountPin), J9.4, J10.6 (VSS), J10.9 (SHIELD), J11.1, J11.MP (MountPin), J12.MP (MountPin), R1.1, R2.1, R7.2, R11.1, R15.2, R16.1, R18.1, R19.1, R20.1, R21.1, R23.1, R24.2, R25.2, R26.2, R28.1, R38.1, TP8.1, TP10.1, TP11.1, TP13.1, U1.5 (GND), U2.2 (GND), U3.2 (GND), U4.5 (GND), U11.C2 (VSS), U11.E4 (VSS), U11.E5 (VSS), U11.E6 (VSS), U11.G1 (VSSA), U11.J1 (VSS), U13.1 (GND), U13.7 (GND), U14.4 (GNDIO), U14.6 (GND), U14.7 (PS), U15.4 (GNDIO), U15.6 (GND), U15.7 (PS), U16.4 (GND), U19.3 (GND), Y1.2 (GND)
unnamed: C17.1, R8.2
unnamed: C21.1, R10.2
unnamed: C27.2, U11.E7 (VCAP)
unnamed: C28.2, U11.F8 (VCAP)
unnamed: D6.2 (A), Q1.1 (G), R7.1
unnamed: D8.1 (K), R18.2
unnamed: D9.1 (K), R19.2
unnamed: D10.1 (K), R20.2
unnamed: D11.1 (K), R21.2
unnamed: D12.1 (K), R24.1
unnamed: D13.1 (K), R25.1
unnamed: D14.1 (K), R26.1
unnamed: J1.A5 (CC1), R2.2
unnamed: J1.B5 (CC2), R1.2
unnamed: R9.2, R11.2, R13.1
unnamed: R12.2, R16.2, R17.1
unnamed: R8.1, U1.4 (BST)
unnamed: R3.2, U1.3 (EN/SYNC)
unnamed: R9.1, U1.1 (FB)
unnamed: R4.2, U1.8 (PG)
unnamed: C17.2, L1.1, U1.6 (SW)
unnamed: C7.1, R4.1, U1.2 (VCC)
unnamed: R10.1, U4.4 (BST)
unnamed: R5.2, U4.3 (EN/SYNC)
unnamed: R12.1, U4.1 (FB)
unnamed: R6.2, U4.8 (PG)
unnamed: C21.2, L2.1, U4.6 (SW)
unnamed: C10.1, R6.1, U4.2 (VCC)
unnamed: C35.1, U11.A1 (PC14-OSC32_IN), Y2.2
unnamed: C36.1, U11.B1 (PC15-OSC32_OUT), Y2.1
unnamed: BOOT1.2, R28.2, U11.D5 (BOOT0)
unnamed: C30.1, U11.C1 (PH0-OSC_IN), Y1.3 (OUT)
Periph_3V3: C15.1, C18.1, C20.1, C37.1, C39.1, C43.2, D9.2 (A), J10.4 (VDD), TP5.1, U3.5 (VOUT), U16.3 (IO2), U16.7 (IO3), U16.8 (VCC)
System_4V5: C5.1, C6.1, D5.1 (K), D7.1 (K), U2.1 (VIN), U2.3 (EN), U3.1 (VIN), U3.3 (EN)
System_5V: C23.1, C24.1, D7.2 (A), D10.2 (A), J3.2, J4.2, J5.2, J7.2, J11.2, L1.2, R13.2, TP3.1, TP4.1, TP6.1, TP7.1, TP9.1
VCC_24V: C1.1, C2.1, C3.1, C4.1, C8.1, D6.1 (K), Q1.2 (S), R3.1, R5.1, R14.1, TP1.1, U1.7 (IN), U4.7 (IN)
VCC_BAT: C12.1, C13.1, D3.2 (A2), J6.7, Q1.3 (D)

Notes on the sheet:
9V 3A output
power up singal to tirgger qgroundcontrol bootloader sync
6.3V 耐压即可
7.68kR 5V output
SPL06 Baro I2C1
BAT_Voltage_Detection
If 0R is connected UART5 RX is used as SBUS
IMU BMI088 SPI1
防反接
SDO To VSS ADDR:0x1110110 SDO To VDDIO ADDR:0x1110111 CSB To VDDIO In I2C Mode
If want to utilize UART8 in PX4, make UART6 as the debug port
2S-6S input to 5V
冲击保护
3.3V 500mA MCU IMU Power
5V to Periph_VCC
Sbus
9V/10V to drive CAM
此处的电流一般不会超过5A
没有使用，将滤波工作交给O3
Cap should be 10% X5R Res should be 1% 注释电压都是最低要求 或者这个封装能找到的可用的 板子适配DJI O3 天空端
IMU BMI088 SPI4
Buzzer
FRAM / QSPI
ADR for accel data ready GDR for gyro data ready ACS for accel cs GCS for gyro cs
BAT power
3.3V 500mA TF-Card QSPI OSD
IO GH2.5
MCU
BAT power protection
SD_CARD
DJI O3
5V 3A output
3.54k output 10V 4.02k output 9V 2.9k for 12V
5V to Core_VCC
Type-C power
2S-6S input to 9V

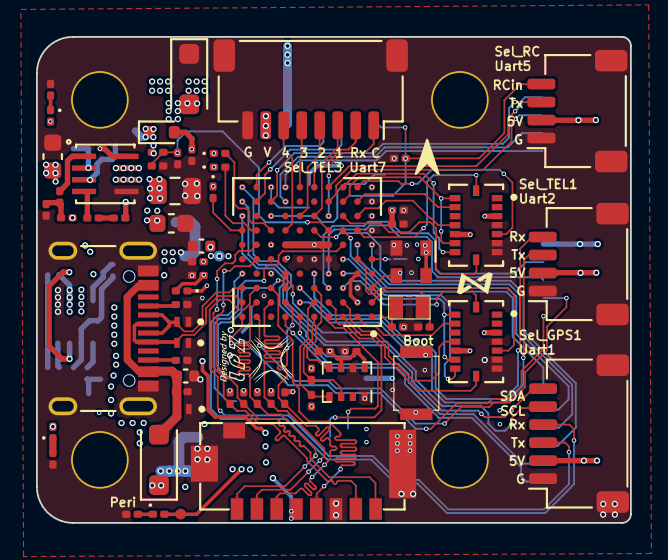
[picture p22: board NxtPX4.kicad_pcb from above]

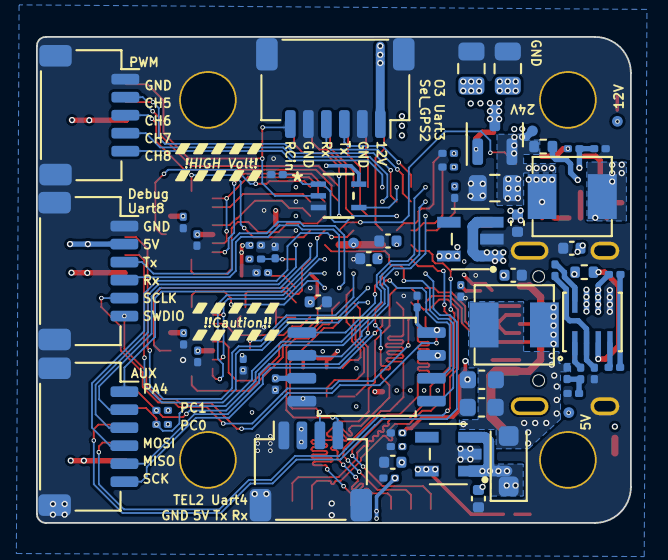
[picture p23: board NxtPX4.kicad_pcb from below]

Board: 4 copper layers, 33.0 x 27.0 mm, 137 parts (65 on the bottom side), 109 nets.

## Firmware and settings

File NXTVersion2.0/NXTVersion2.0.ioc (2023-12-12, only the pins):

Mcu.UserName=STM32H743VIHx
PA0.GPIO_Label=SPI1_ADR
PA0.Signal=GPXTI0
PA1.GPIO_Label=SPI1_GDR
PA1.Signal=GPXTI1
PA10.Signal=USART1_RX
PA11.Signal=USB_OTG_FS_DM
PA12.Signal=USB_OTG_FS_DP
PA2.GPIO_Label=SPI1_ACS
PA2.Signal=GPIO_Output
PA3.GPIO_Label=SPI1_GCS
PA3.Signal=GPIO_Output
PA4.GPIO_Label=AUX3
PA4.Signal=GPIO_Output
PA5.Signal=SPI1_SCK
PA6.Signal=SPI1_MISO
PA7.Signal=SPI1_MOSI
PA9.Signal=USART1_TX
PB0.Signal=S_TIM3_CH3
PB1.Signal=S_TIM3_CH4
PB10.Signal=S_TIM2_CH3
PB11.Signal=S_TIM2_CH4
PB12.Signal=UART5_RX
PB13.Signal=UART5_TX
PB14.Signal=SPI2_MISO
PB15.GPIO_Label=LED_R
PB15.Signal=GPIO_Output
PB2.Signal=SPI3_MOSI
PB5.GPIO_Label=BARO_DR
PB5.Signal=GPXTI5
PB6.Signal=I2C1_SCL
PB7.Signal=I2C1_SDA
PB8.Signal=UART4_RX
PB9.Signal=UART4_TX
PC0.GPIO_Label=AUX2
PC0.Signal=GPIO_Output
PC1.GPIO_Label=AUX1
PC1.Signal=GPIO_Output
PC10.Signal=SDMMC1_D2
PC11.Signal=SDMMC1_D3
PC12.Signal=SDMMC1_CK
PC13.GPIO_Label=SPI4_ACS
PC13.Signal=GPIO_Output
PC2_C.GPIO_Label=SPI4_GCS
PC2_C.Signal=GPIO_Output
PC3_C.Signal=SPI2_MOSI
PC4.Signal=ADCx_INP4
PC5.GPIO_Label=ADC_I
PC5.Signal=ADCx_INP8
PC6.Signal=USART6_TX
PC7.Signal=USART6_RX
PC8.Signal=SDMMC1_D0
PC9.Signal=SDMMC1_D1
PD0.Signal=GPIO_Input
PD11.GPIO_Label=LED_G
PD11.Signal=GPIO_Output
PD12.Signal=I2C4_SCL
PD13.Signal=I2C4_SDA
PD15.GPIO_Label=LED_B
PD15.Signal=GPIO_Output
PD2.Signal=SDMMC1_CMD
PD3.Signal=SPI2_SCK
PD4.GPIO_Label=FRAM_CS
PD4.Signal=GPIO_Output
PD5.Signal=USART2_TX
PD6.Signal=USART2_RX
PD8.Signal=USART3_TX
PD9.Signal=USART3_RX
PE0.Signal=UART8_RX
PE1.Signal=UART8_TX
PE11.Signal=S_TIM1_CH2
PE13.Signal=S_TIM1_CH3
PE14.Signal=S_TIM1_CH4
PE2.Signal=SPI4_SCK
PE3.Signal=GPXTI3
PE4.GPIO_Label=SPI4_GDR
PE4.Signal=GPXTI4
PE5.Signal=SPI4_MISO
PE6.Signal=SPI4_MOSI
PE7.Signal=UART7_RX
PE8.Signal=UART7_TX
PE9.Signal=S_TIM1_CH1

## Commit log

2023-01-08 Init:Init NxtPX4 hardware repo
    [CAP_ABS07-32_768KHZ-T_ABR.step, CSP-USC16-TR--3DModel-STEP-468060.STEP, DFN1006-2_SOD882_NEX.step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]
2023-02-06 [Feat][other]:Release first version of hardware design
    [CAP_ABS07-32_768KHZ-T_ABR.step, CSP-USC16-TR--3DModel-STEP-468060.STEP, DFN1006-2_SOD882_NEX.step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]
2023-03-03 [Feat][other]:Release V1.0 hardware design all need fucntion test pass
    [CAP_ABS07-32_768KHZ-T_ABR.step, CSP-USC16-TR--3DModel-STEP-468060.STEP, DFN1006-2_SOD882_NEX.step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]
2023-03-03 [Fix][other]:Upgrade for JLC manufacturer
    [CAP_ABS07-32_768KHZ-T_ABR.step, CSP-USC16-TR--3DModel-STEP-468060.STEP, DFN1006-2_SOD882_NEX.step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]
2023-03-23 [Fix][hardware]:v1.1.0 change esc pinout order
    [CAP_ABS07-32_768KHZ-T_ABR.step, CSP-USC16-TR--3DModel-STEP-468060.STEP, DFN1006-2_SOD882_NEX.step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]
2023-03-26 [Doc][other]:readme add uart define
2023-03-26 [Doc][readme]: add v1.1.0 board img
2023-05-04 [Feat][Release]:Release v1.2.0 hardware
    [01x05_sh1.0_hori.step, CAP_ABS07-32_768KHZ-T_ABR.step, CSP-USC16-TR--3DModel-STEP-468060.STEP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]
2023-12-12 [Feat][new version]: update hardware v2.0 Dual
    [01x05_sh1.0_hori.step, CAP_ABS07-32_768KHZ-T_ABR.step, CSP-USC16-TR--3DModel-STEP-468060.STEP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]
2024-07-04 [Rlease][Dual]: Update logo for Dual version
    [01x05_sh1.0_hori.step, CAP_ABS07-32_768KHZ-T_ABR.step, CSP-USC16-TR--3DModel-STEP-468060.STEP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]
